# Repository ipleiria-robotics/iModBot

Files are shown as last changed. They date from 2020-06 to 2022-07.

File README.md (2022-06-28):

# Apresentação do Projeto 
Este projeto iModBot consiste num robô modular de baixo custo que pode ser programado através de liguagem de programação por blocos e/ou através de linguagem C/C++. Este projeto dispõe de uma biblioteca para facilitar o controlo do robô. 

A programação por blocos divide-se em 4 níveis, para facilitar a aprendizagem do utilizadores. Os níveis são os seguintes:
 - Nível Iniciante -> É possível colocar o robô a efetuar uma terefa com 1 a 2 blocos.
 - Nível Normal -> O utilizador tem mais controlo sob o movimento do robô, dispõe apenas da função loop.
 - Nível Médio -> O utilizador pode agora colocar blocos na função Setup e Loop.
 - Nível Avançado -> O utilizador dispõe de todas as funções da biblioteca e necessita de configurar todos os aspetos do robô.
    
ROBOT

# Como transferir ficheiros do GitHub
No GitHub não é possível transferir qualquer ficheiro individualmente. É recomendado transferir todas as pastas e ficheiros presentes neste projeto. Para tal siga as instruções abaixo:

Comece por transferir todos os ficheiros no formato .zip


Abra a localização do ficheiro .zip transferido e use um programa para extrair os conteudos


Por fim irá obter um conjunto de pastas e ficheiros organizados da mesma maneira que se encontram neste repositório.



# Elaboração do Projeto
**1º Passo do Projeto**

Para montar o robô basta seguir o documento 4_Guia_de_montagem_offline ([3_Documentacao/3-4_Guia_de_montagem_offline.pdf](https://github.com/ipleiria-robotics/iModBot/blob/master/3_Documentacao/3-4_Guia_de_montagem_offline.pdf)) que mostra como montar ou então assistir o video [iModBot@ipleiria.pt guia de montagem](https://www.youtube.com/watch?v=i4wFh0GqzkM&feature=emb_logo). Este documento também inclui uma listagem de componentes
que serão necessários para a sua montagem. Para perceber melhor o que faz cada componente do robô pode ler o manual técnico ([3_Documentacao/3-5_Manual_Tecnico_iModBot.pdf](https://github.com/ipleiria-robotics/iModBot/blob/master/3_Documentacao/3-5_Manual_Tecnico_iModBot.pdf)) que explica vários aspetos do robô. 

Lista de material:
 * ESP32 wroom32 devkit ; 
 <p align="center">
  
</p>

 * l293d 4 channel module ;
 <p align="center">
  
</p>   

 * 2x LM393 speed sensor ; 
 <p align="center">
  
</p> 

 * BFD-1000 5CH ;
  <p align="center">
  
</p>   

 * HC-SR04 ;
  <p align="center">
  
</p> 

 * I2C level shifter ; 
 <p align="center">
  
</p> 

 * TP4056 ; 
 <p align="center">
  
</p> 

 * MT3608 ; 
 <p align="center">
  
</p> 

 * li-ion rechargable battery 2500 mAh ; 
 <p align="center">
  
</p> 

 * 2x Breadboard 400 ; 
 <p align="center">
  
</p> 

 * Jumper wire male male, Jumper wire male female ; 
 <p align="center">
  
</p> 

 * 2wd smart robot kit . 
 <p align="center">
  
</p> 

**2º Passo do Projeto** 
 
 Downloads:
 
- Biblioteca iModBot.zip ([4_Biblioteca/iModBot.zip](https://github.com/ipleiria-robotics/iModBot/blob/master/4_Biblioteca/iModBot.zip)) e descompacta o ficheiro. Anotação 2020-06-25 170046

- Software Arduino IDE na [pagina do Arduino](https://www.arduino.cc/en/main/software), instale a versão que se adequa ao seu equipamento, para windows recomendamos a opção "Windows installer, for windows 7 and up". 
 -- Tenha em atenção que os conteudos do projeto foram desenvolvidos e testados na versão Arduino IDE 1.8.12, os mesmos deverão continuar ser compatíveis com as versões mais recentes deste software.
       <p align="center">
  
</p> 

- Ficheiro java do ArduBlock ([5_AduBlock/ardublock-beta-20200614.jar](https://github.com/ipleiria-robotics/iModBot/blob/master/5_AduBlock/ardublock-beta-20200614.jar)).

Anotação 2020-06-25 172512

**3º Passo do Projeto**

Ler e seguir os tutoriais para configurar o Arduíno:
 - Configurar Arduíno IDE para o ESP32; ([3_Documentacao/3-1_Como_comunicar_com_o_ESP32.pdf](https://github.com/ipleiria-robotics/iModBot/blob/master/3_Documentacao/3-1_Como_comunicar_com_o_ESP32.pdf))

 - Configurar ArduBlock no Arduíno IDE; ([3_Documentacao/3-2_Como_instalar_ArduBlock_no_Arduino_IDE.pdf](https://github.com/ipleiria-robotics/iModBot/blob/master/3_Documentacao/3-2_Como_instalar_ArduBlock_no_Arduino_IDE.pdf))

 - Como instalar bibliotecas no Arduíno IDE. ([3_Documentacao/3-3_Como_instalar_bibliotecas_no_Arduino_IDE.pdf](https://github.com/ipleiria-robotics/iModBot/blob/master/3_Documentacao/3-3_Como_instalar_bibliotecas_no_Arduino_IDE.pdf))

# Documentação

Após ter o Arduino IDE e o ArduBlock instalados pode usufruir dos tutoriais disponibilizados. Estes tutoriais ensinam a trabalhar com o robô sendo os mesmos divididos em duas categorias: tutoriais para ArduBlock e tutoriais para Arduino IDE.

**Documentação do ArduBlock**

Os [4 níveis](https://github.com/ipleiria-robotics/iModBot/tree/master/1_Tutoriais/1-1_Tuturiais_para_ArduBlock) a baixo irão facilitar e guiar como deve de utilizar cada bloco e como criar um programa.

- [Nivel Iniciante;](https://github.com/ipleiria-robotics/iModBot/blob/master/1_Tutoriais/1-1_Tuturiais_para_ArduBlock/Tutorial_1_-_Nivel%20iniciante/Nivel_iniciante.pdf)

- [Nivel Normal;](https://github.com/ipleiria-robotics/iModBot/blob/master/1_Tutoriais/1-1_Tuturiais_para_ArduBlock/Tutorial_2_-_Nivel_Normal/Nivel_Normal.pdf)

- [Nivel Médio;](https://github.com/ipleiria-robotics/iModBot/blob/master/1_Tutoriais/1-1_Tuturiais_para_ArduBlock/Tutorial_3_-_Nivel_Medio/Nivel_Medio.pdf)

- [Nivel Avançado;](https://github.com/ipleiria-robotics/iModBot/blob/master/1_Tutoriais/1-1_Tuturiais_para_ArduBlock/Tutorial_4_-_Nivel_Avancado/Nivel_Avancado.pdf)

Existe um conjunto de atividades para cada nível. Após ler a documentação de um nível poderá realizar a atividade correspondente  ao mesmo em [2_Atividades/2-1_Atividades_para_ArduBlock/](https://github.com/ipleiria-robotics/iModBot/tree/master/2_Atividades/2-1_Atividades_para_ArduBlock).

**Documentação do Arduino IDE**

Depois de já ter realizado os tutoriais do ArduBock deverá ter uma noção melhor de como programar no Arduino IDE. Também elaboramos alguns tutoriais e atividades para facilitar a aprendizagem,

- [Tutorial 1 - Movimento;](https://github.com/ipleiria-robotics/iModBot/blob/master/1_Tutoriais/1-2_Tutoriais_para_Arduino_IDE/Tutorial_1_-_Movimento/Tutorial_1_iModBot_-_Movimento.pdf)

- [Tutorial 2 - Sensores;](https://github.com/ipleiria-robotics/iModBot/blob/master/1_Tutoriais/1-2_Tutoriais_para_Arduino_IDE/Tutorial_2_-_Sensores/Tutorial_2_iModBot_-_Sensores.pdf)

- [Tutorial 3 - Seguir trajeto.](https://github.com/ipleiria-robotics/iModBot/blob/master/1_Tutoriais/1-2_Tutoriais_para_Arduino_IDE/Tutorial_3_-_Seguir_trajeto/Tutorial_3_iModBot_-_Seguir%20trajeto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)

As atividades para cada tutorial estão disponíveis em [/2_Atividades/2-2_Atividades_para_Arduino_IDE/
](https://github.com/ipleiria-robotics/iModBot/tree/master/2_Atividades/2-2_Atividades_para_Arduino_IDE).

# Editar o ArduBlock

Caso tenha interesse em criar um bloco deve seguir os passos neste pasta [5.Ardublock](https://github.com/ipleiria-robotics/iModBot/blob/master/5_AduBlock/README.md)

# Realidade Aumentada

Utilizando o motor de jogos Unity3d, ROS2 e a nossa biblioteca para o robô, cria o teu mundo virtual, projeta-o no mundo real e vê o robô a interagir com ele.
Esta funcionalidade ainda está em desenvolvimento sendo que por agora ainda é muito limitada. 

# Controladores remotos

Com os controladores das consolas populares PS3 e PS4, consegue controlar o robot à distância via bluetooth. A biblioteca é fácil de instalar e apenas necessita de um programa, o Arduino IDE. Basta colocar valores desejados no código, tanto como sensibilidade de direção, aceleração dos motores, velocidade máxima, e muito mais!

# Autores
 
- Abel Teixeira   - estudante do [Politécnico de Leiria](https://www.ipleiria.pt/cursos/) do curso TeSP em Eletrónica e Redes de Telecomunicações, GitHub: [Ab-Tx](https://github.com/Ab-Tx)
- Samuel Lourenço - estudante do [Politécnico de Leiria](https://www.ipleiria.pt/cursos/) do curso TeSP em Automação, Robótica e manutenção Industrial, GitHub: [SamueLourenc0](https://github.com/SamueLourenc0)
- Nelson Henriques - estudante do [Politécnico de Leiria](https://www.ipleiria.pt/cursos/) do curso TeSP em Automação, Robótica e manutenção Industrial, GitHub: [NetchoExtreme](https://github.com/NetchoExtreme)
- Paulo Sousa - estudante do [Politécnico de Leiria](https://www.ipleiria.pt/cursos/) do curso TeSP em Eletrónica e Redes de Telecomunicações, GitHub [DimitriOnLSD](https://github.com/DimitriOnLSD)

## Orientado por:
- Luís Conde - [Politécnico de Leiria](https://www.ipleiria.pt), GitHub: [Luís Conde](https://github.com/conde-ISR-UC-PT)
- Carlos Neves - [Politécnico de Leiria](https://www.ipleiria.pt), [INESC-Coimbra](http://inescc.estg.ipleiria.pt/), GitHub: [Carlos Neves](https://github.com/carlos-neves)

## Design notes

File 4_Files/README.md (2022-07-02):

# Files

Folder tree:
```
4_Files
├── 4-1_PCB_Files/        // 2 PCB versions
├── 4-2_3D_Files/         // Cases for the batteries and side motor supports
├── 4-3_Libraries/        // Dualshock libraries for remote controllers and iModBot library for various other functions
└── 4-4_ArduBlock/        // ArduBlock file for Arduino IDE and ArduBlock-Workspace for editing or creating blocks
```
## Software

To be able to edit source files inside the folders, you will need the following programs:

`Eclipse IDE` This is used to edit the ArduBlock-Workspace file. In there, you can edit or create blocks, change default values or create new ones, change blocks image, etc. Tutorials for installing this program, along with JDK and maven, can be found in the 3-Documents folder.

`EAGLE` This is used to open and edit the first PCB version. 

`Proteus 8.10` This is used to open and edit the second PCB version. Keep in mind that this file can't be opened in previous versions of proteus, like 8.9.

`Fusion 360` `SolidWorks` `SketchUp Pro 2021` These can be used to open and edit the .F3D, .step and .skp files inside Battery_Case_3D folder.

`Visual Studio Code` This is used to edit the .h and .cpp files inside both libraries.

`Arduino IDE` This is used to upload the code to the ESP32.

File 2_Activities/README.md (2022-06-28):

# Activities

Activities and their solutions are provided. 
These are divided into two categories:
- Activities for ArduBlock;
- Activities for Arduino IDE.

Tutorials for each activity are available at [1_Tutorials](https://github.com/ipleiria-robotics/iModBot/tree/master/1_Tutoriais)

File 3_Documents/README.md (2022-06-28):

# Documents

Inside this folder you will find documentation for the various project aspects and their respective DOCX files for editing:

- `src`
  - PDF source files.

- **3-00_iModBot_Components_List.xlsx**
  - Supplies the list components used in iModBot, with some of their respective buy stores and prices.

- **3-01_iModBot_Tech_Manual.pdf**
  - Describes the components used in the project, the functions provided by the library and other aspects.

- **3-02_iModBot_Assembly_And_Software_Installation_Tutorial.pdf**
  - Teaches you how to install the necessary tools and how to assemble the robot.

- **3-03_iModBot_Offline_Assembly_Guide.pdf**
  - Provides a list of components and shows the connections that must be made between the components.

- **3-04_Add_ESP32_Arduino_IDE.pdf**
  - Explains how to connect the ESP32 development board to the Arduino IDE software.

- **3-05_Add_ArduBlock_Arduino_IDE.pdf**
  - Explains how to install ArduBlock in the Arduino IDE software.
  
- **3-06_Add_Arduino_IDE_Libraries.pdf**
  - Explains how to install libraries in the Arduino IDE software.
  
- **3-07_Edit_ArduBlock_Files.pdf**
  - It teaches how to install all the tools needed to edit the ArduBlock Workspace.

- **3-08_Create_ArduBlock_Blocks.pdf**
  - Teaches how to create a block in ArduBlock using the Eclipse IDE.

- **3-09_Add_Eclipse_IDE_Libraries.pdf**
  - Explains how to add libraries to the Eclipse IDE software.

- **3-10_Update_JDK.pdf**
  - Guide to update the Java version for using the Eclipse IDE.

- **3-11_Openblock_Error_Tutorial.pdf**
  - Troubleshooting guide for error in openblocks install.

- **3-12_Basic_Eletronics_Assembly_Guide.pdf**
  - A basic assembly guide is provided to acquaint you with the Breadboard and how it works when mounting electronic boards in this tool.

- **3-13_Remote_Bluetooth_Dualshock.pdf**
  - A tutorial is provided on how to set up the code to pair a dualshock 3 or 4 controller to control the robot remotely via Bluetooth.

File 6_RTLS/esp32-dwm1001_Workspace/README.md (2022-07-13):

# esp32-dwm1001_Workspace

*Note that the examples below consist in very basic application using the UWB features of the DWM1001C. These examples are not intended to be used in a commercial application and may not comply with regulation requirements.*

*Advanced firmware for DWM1001C that would comply with regulations can be found on https://www.decawave.com/product/dwm1001-module/*

## Overview

This project contains C simple examples for DWM1001 hardware and its derivatives, such as the DWM1001-DEV board and Development Kit Board MDEK1001.

The DWM1001 module is a Ultra Wideband (UWB) and Bluetooth hardware based on DecaWave's DW1000 IC and Nordic Semiconductor nrF52832 SoC. It allows to build a scalable Two-Way-Ranging (TWR) RTLS systems with up to thousands of tags. 

The DWM1001-DEV is a development board for the DWM1001 module. It contains an integrated Jlink to facilitate development and debbuging.
For more information about DWM1001, please visit www.decawave.com.

The C simple examples allow user to discover the key functionalities offered by the DWM1001 and UWB. These examples are customized for DWM1001-DEV, and some modifications will be necessary to port them to other DWM1001 based hardware (in particular LED and button interface)

The project is built as follow : 
```
esp32-dwm1001_Workspace/
├── boards             // DWM1001-DEV board specific definitions
├── deca_driver        // DW1000 API software package 2.04 
├── examples           // C simple examples 
│   ├── ss_twr_init    // Single Sided Two Way Ranging Initiator example
│   ├── ss_twr_resp    // Single Sided Two Way Ranging Responder example
│   └── twi_accel      // LIS2DH12 accelerometer example with Two Wire interface 
├── nRF5_SDK_14.2.0    // Nordic Semiconductor SDK 14.2 for nrF52832
├── ESP32_UART_DWM1001 // UART communication interface with ESP32-DevKitC-V4
└── README.md
```
For more information about nrF52832 and nrF SDK, please visit http://infocenter.nordicsemi.com/

## Supported IDE

The examples are ready to use with the following IDE :
* Segger Embedded Studio (SES)
* Keil KEIL µVision

## Segger Embedded Studio

Each example contains a emproject project file for SES. The examples compile and load cleanly to the DWM1001.   
The project was created with the SES version V3.34a. 

SES has a free license for nrF52832 development. Consequently, this IDE can be used without any limitation for DWM1001 development.

For more information regarding Segger Embedded Studio, please visit https://www.segger.com/products/development-tools/embedded-studio/

For more information about free license for nrF52832, please read https://www.nordicsemi.com/News/News-releases/Product-Related-News/Nordic-Semiconductor-adds-Embedded-Studio-IDE-support-for-nRF51-and-nRF52-SoC-development

### SES : Additional Package

When using SES IDE, you will need to install the following package :

Package                                                                                                                           
CMSIS 5 CMSIS-CORE Support Package (version 5.02)                                                                           
CMSIS-CORE Support Package (version 4.05)                                                                           
Nordic Semiconductor nRF CPU Support Package (version 1.06)                                                                           

They can be install from SES itself, through the package manager in the tools menu. 

## KEIL µVision IDE

Each example contains a µVision5 project file for Keil µVision IDE. The examples compile and load cleanly to the DWM1001.
The project was created with the KEIL uVision version V5.24.2.0. 

Keil µVision has a free license for project up to 32KB. For more information regarding Keil µVision, please visit http://www2.keil.com/mdk5/uvision/

### µVision Error: Flash Download failed - "Cortex-M4"

This error can be observed if there is a memory conflict between the binary to load and the current firmware on the target hardware. This issue can be easily fixed by fully erasing the target device 's flash memory. Keil µVision cannot perform a full erase and the following free tool can be used :

* J-flash lite 
* nrfjprog command line script

For more information about the issue, please see :

https://devzone.nordicsemi.com/f/nordic-q-a/18278/error-flash-download-failed---cortex---m4-while-flashing-softdevice-from-keil-uvision-5

## Example Details 

The SS-TWR scheme can be implemented using two DWM1001 modules, the first one programmed as an initiator and the second one as a responder.

### Single Sided Two Way Ranging -- Initiator

This example contains the source code for the initiator. The initiator will send a frame, wait for the response from the receiver, calculate the distance and output it on the UART (can be observed on a serial terminal)

```
dwm1001-keil-examples/examples/ss_twr_init/
├── config                    // Contains sdk_config.h file for nrF SDK 14.2 customization
├── main.c                    // Initialization and main program
├── ss_init_main.c            // Single sided initiator core program
├── UART                      // Uart 
├── SES
│   └── ss_twr_init.emProject // Segger Embedded Studio project
└── Keil uvision
     └── ss_twr_init.uvprojx  // Keil uvision project

```
The application function is detailed in the main.c and the ss_init_main.c files. 

Calibration may be necessary in order to have an accurate measurement. It can be done by adjusting the antenna delay which is hardware dependent. 

### Single Sided Two Way Ranging -- Responder

This example contains the source code for the responder. The receiver will receive a frame from the initiator and send the corresponding answer.

```
dwm1001-keil-examples/examples/ss_twr_resp/
├── config                    // Contains sdk_config.h file for nrF SDK 14.2 customization
├── main.c                    // Initialization and main program
├── ss_resp_main.c            // Single sided responder core program
├── SES
│   └── ss_twr_resp.emProject // Segger Embedded Studio project
└── Keil uvision
     └── ss_twr_resp.uvprojx  // Keil uvision project
```
The application function is detailed in the main.c and the ss_resp_main.c files. 

Calibration may be necessary in order to have an accurate measurement. It can be done by adjusting the antenna delay which is hardware dependent. 

### Two Wire Interface Accelerometer

This example implements a TWI between the LIS2DH12 and the nrF52832. 
The blue led will be on when a motion is detected by the LIS2DH12. It also reports the accelerometer state on the UART.

```
dwm1001-keil-examples/examples/twi_accel/
├── config                    // Contains sdk_config.h file for nrF SDK 14.2 customization
├── LIS2DH12                  // LIS2DH12 (accelerometer) low level driver and api
├── main.c                    // Initialization and main program
├── TWI                       // TWI
├── UART                      // Uart
├── SES
│   └── twi_accel.emProject // Segger Embedded Studio project
└── Keil uvision
     └── twi_accel.uvprojx  // Keil uvision project
```
The application function is detailed in the main.c file.

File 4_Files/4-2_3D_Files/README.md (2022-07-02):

# 3D Battery cases

__Prototype 1__

`bat case v9.step`
Features the most recent version for single battery case for this prototype.

__Prototype 2__

`Battery_Holder.skp`
Features the most recent version for single battery case for this prototype.

`Battery_Holder_Stacked.skp`
Features an inside battery stacking with no middle layer. Simple use and faster printing but not recommended.

`Battery_Holder_Slot.skp`
Features an inside battery stacking with removable middle layer.

__Others__

`motors_side_support_v3.stl`
3D printable piece for side supports in iModBot chassis.

## Information

This folder contains all cases used in iModBot for the batteries. All outter holes dimensions are specifically designed for the iModBot chassis alone. 

Sterolithography files (STL) can be opened directly with CURA software for 3D printing. 

SketchUp (SKP), Fusion 360 (F3D) and Standard for the Exchange of Product Data (STEP) files are the given open-source files. SkethUp files were saved with 2021 version.

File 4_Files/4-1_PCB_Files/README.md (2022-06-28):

# PCB Files

__EAGLE__ and __KiCAD__

`iModBot_EAGLE_rev_1.rar`
First version of iModBot PCB with 1 battery input and Step-up to 7V.

`iModBot_EAGLE_REV_2.rar`
Second version of iModBot PCB with 2 batteries input, no Step-up and better organized schematic. This version does not include board files.

__Proteus 8.10__

`imodbot_rev_2.pdsprj`
PCB's first revision featuring an additional battery and removed the Step-up, with better testpoints.

`imodbot_rev_2-CADCAM.rar`
Contains CADCAM data for the proteus PCB.

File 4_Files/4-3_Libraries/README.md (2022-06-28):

# Dualshock and iModBot Libraries

These libraries were written in C/C++ programming language. You will find instructions on how to install these and upload them to the ESP32 inside the  [3-Documents](https://github.com/DimitriOnLSD/iModBot/tree/master/3_Documents) folder. Inside you can also find information regarding the robots' various functions.

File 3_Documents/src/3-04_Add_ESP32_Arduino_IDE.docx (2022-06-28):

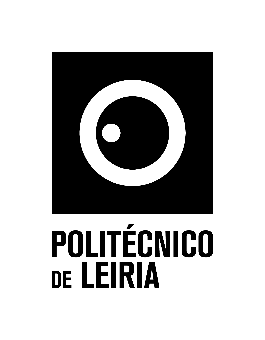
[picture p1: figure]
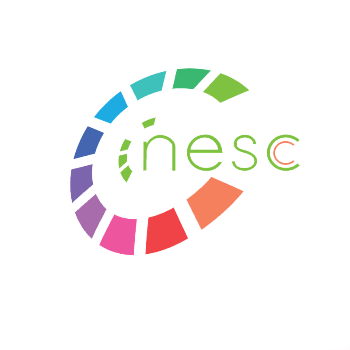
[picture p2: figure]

| Guia de montagem iModBot@ipleiria.pt

Tutorial de como comunicar com o ESP32 através do programa Arduíno IDE

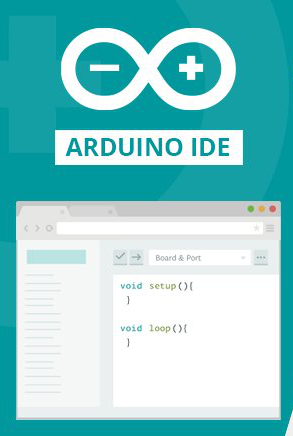
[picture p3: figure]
Tutorial of Programming ESP32 in Arduino IDE
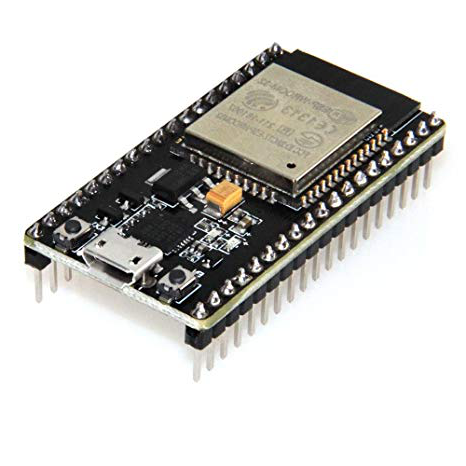
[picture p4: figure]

comunicar

Com o programa Arduino IDE aberto, siga os vários passos para configurar o Arduino IDE para comunicar o ESP32.

Também foi feito um vídeo para o caso de surgir alguma dúvida:

https://www.youtube.com/watch?v=xiqXJj58ynI

1. Com o Arduino IDE aberto, abra a janela “preferences” (File → Preferences);
2. Prima o botão que tem uma figura de uma pasta aberta (3) e cole o link:

https://dl.espressif.com/dl/package_esp32_index.json ;

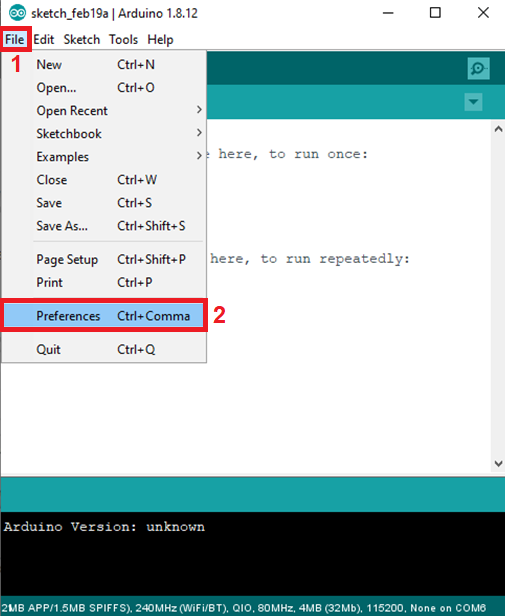
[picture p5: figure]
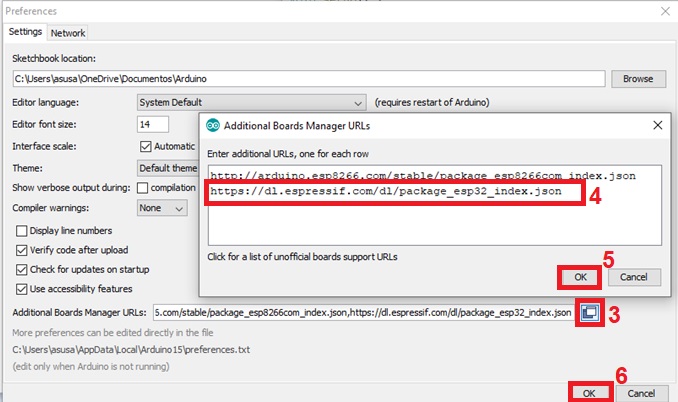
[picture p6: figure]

3. Na janela “Boards Manager…” escreva “ESP32” e instale a placa (Tools => Board=> Boards Manger…) ;

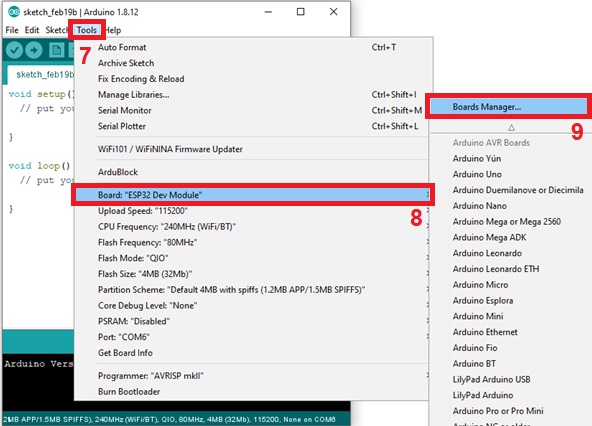
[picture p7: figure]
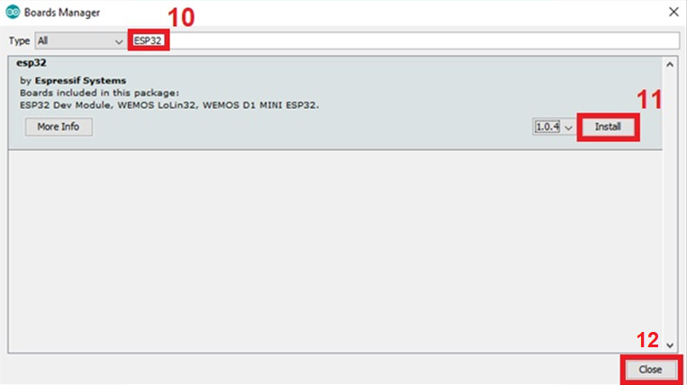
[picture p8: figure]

4. Ainda com a o separador “Tools” aberto configure os seguintes pontos:

“Board” escolha a placa compatível, neste caso “ESP32 Dev Module”;

“Upload Speed:” escolha uma das opções, é recomendado 115200;

“Port:” escolha a porta COM onde a placa de desenvolvimento ESP32 foi ligada, geralmente é o maior número apresentado;

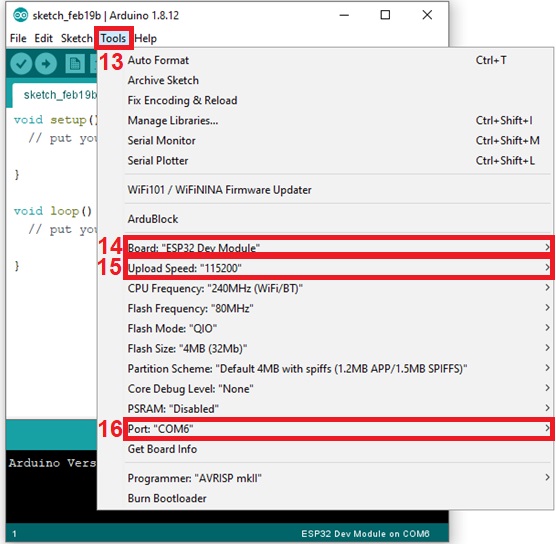
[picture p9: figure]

iModBot@ipleiria.pt Página 1 de 4

Autor: Samuel Domingos Lourenço 19 de fevereiro de 2020 2

Politécnico de Leiria 2019/2020

INSTITUTO POLITÉCNICO DE LEIRIA ESCOLA SUPERIOR DE TECNOLOGIA E GESTÃO

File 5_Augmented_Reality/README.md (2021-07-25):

# Realidade Aumentada

Utilizando o motor de jogos Unity3d, ROS2 e a nossa biblioteca para o robô, cria o teu mundo virtual, projeta-o no mundo real e vê o robô a interagir com ele.

Esta funcionalidade ainda está em desenvolvimento sendo que por agora ainda é muito limitada.

## Requisitos

 - Ubuntu 20.04 (nativo ou Virtual)
 -- Consulta o documento [Tutorial_SetUp_VM](https://github.com/ipleiria-robotics/iModBot/blob/master/6_Realidade_Aumentada/Tutorial_SetUp_VM.pdf) para o instalares numa Virtual Machine (é recomendado a instalação nativa).
 
  - Docker  
 -- Consulta o documento [Tutorial_docker](https://github.com/ipleiria-robotics/iModBot/blob/master/6_Realidade_Aumentada/Tutorial_docker.pdf) para o instalares e perceberes o seu funcionamento.

## Utilização

1. Abre um terminal na pasta [iModBot-Docker](https://github.com/ipleiria-robotics/iModBot/tree/master/6_Realidade_Aumentada/iModBot-Docker).
   
2. Cria a imagem Docker (este passo demora algum tempo).
    ```bash
    $ ./build-docker-image.bash
    ```
3. Inicia a imagem criada.
    ```bash
    $ ./run-docker-container
    ```
4.  Abre o `VScode`.
    ```bash
    $ code
    ```
	  --  Instala a  extensão PlatformIO e abre a pasta [VScode_Workspace\ESP32-ROS2_iModBot](https://github.com/ipleiria-robotics/iModBot/tree/master/6_Realidade_Aumentada/iModBot-Docker/VScode_Workspace/ESP32-ROS2_iModBot), coloca o id e a palavra pass da tua rede Wifi e o IP do container.
	  -- Faz Upload do programa para o ESP32.
	  -- Guarda as alterações e fecha o VScode.
    
5. Inicia o `Unity Hub` e instala o editor mais recente e abre o projeto que se encontra na pasta [iModBot-Docker\Unity_Workspace](https://github.com/ipleiria-robotics/iModBot/tree/master/6_Realidade_Aumentada/iModBot-Docker/Unity_Workspace/).
    ```bash
    $ cd unity && ./UnityHub.AppImage
    ```
6.  Inicia o ROS2 Node.
- No terminal da maquina nativa que se encontra na pasta iModBot-Docker abre um novo terminal no container.
    ```bash
    $ ./new_bash_in_container
    ```
 - No novo terminal:
    ```bash
    $ cd work/ROS2_Workspace && . install/setup.bash && ros2 run stop_oncollision oncollision
    ```
7. Inicia o controlo remoto (pode ser acedido em qualquer browser desde que esteja na rede local, através do IP que aparece na janela).
- Abre 2 novos terminais no container, como descrito anteriormente.
- No 1º:
    ```bash
    $ cd ros2-web-bridge && export DEBUG=ros2-web-bridge:* && node bin/rosbridge.js
    ```
- No 2º:
    ```bash
    $ cd ros2-web-bridge/demo && http-server -c-1
    ```
 
8. Inicia o MicroXRCEAgent (responsável por estabelecer a comunicação entre o ROS2 e o ESP32) 
- Abre um novo terminal no container.
- Inicia o programa
    ```bash
    $ MicroXRCEAgent udp4 -p 2018
    ```
Está tudo a postos para comecares a tua jornada com a realidade aumentada.
Sempre que quiseres reabrir o container corre o script [start-docker-container](https://github.com/ipleiria-robotics/iModBot/blob/master/6_Realidade_Aumentada/iModBot-Docker/start-docker-container.bash).

Video demostrativo: [https://youtu.be/DlAx3p5d99E](https://youtu.be/DlAx3p5d99E)

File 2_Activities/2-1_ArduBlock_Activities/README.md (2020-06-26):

# Atividades para ArduBlock

Os presentes tutoriais deverão facilitar a compreensão da linguagem de programaçãopor blocos bem como o seu uso no presente projeto.

Pode encontrar os tutoriais associados em [/1_Tutoriais/1-1_Tuturiais_para_ArduBlock/](https://github.com/ipleiria-robotics/iModBot/tree/master/1_Tutoriais/1-1_Tuturiais_para_ArduBlock).

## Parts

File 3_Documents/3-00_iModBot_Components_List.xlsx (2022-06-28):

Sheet: Previsão de custos_IPL
 |  | Dep. Eng. Eletrotécnica - UC de Projeto em Engenharia Eletrotécnica e de Computadores
 |  | Previsão de custos para Projeto
 |  | Título Projeto: | iModroBot
 |  | Orientadores: | Luis Conde Bento, Diogo Baptista, Alexandra Nascimento
 |  | Data: | 2020-12-09
 |  |  |  |  |  |  |  | Link principal
Item | Descrição | Referência | Qtd | Un. | Fornecedor | Preço unitário | Preço total
1 | Jetson Nano Developer Kit |  | 2 |  | sparkfun | 59.00 € | 59.00 €
2 | Espressif ESP32 WLAN Dev Kit Board Development Bluetooth Wifi v1 WROOM32 NodeMCU |  | 4 |  | ebay | 7.85 € | 31.40 € | https://www.ebay.com/itm/Espressif-ESP32-WLAN-Dev-Kit-Board-Development-Bluetooth-Wifi-v1-WROOM32-NodeMCU/253059783728
3 | Módulo De Accionamento Do Motor MINI L293D Arduino Accionamento Do Motor Placa De Expansão Mini-L293D Para Arduino Kit |  | 4 |  | dx | 3.96 € | 15.84 € | https://www.dx.com/p/mini-l293d-arduino-motor-drive-expansion-board-mini-l293d-motor-drive-module-for-arduino-kit-2716648.html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 | https://www.ebay.com/itm/Mini-Motor-Drive-Shield-Expansion-Board-L293D-Module-For-Arduino-UNO-MEGA2560-R3/182057002265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
4 | Placa de sensores infravermelhos IR 74HC14 |  | 4 |  | ptrobotics | 7.44 € | 29.76 € | https://www.ptrobotics.com/sensores-opticos/6248-5-channel-tracking-sensor-module.html
5 | 5Pcs Speed Measurement Sensor Switch Counter Motor Test Groove Coupler Module Geekcreit for Arduino - produtos que funcionam com placas oficiais Arduino |  | 8 |  | Banggood | 4.67 € | 37.36 € | https://pt.banggood.com/5Pcs-Speed-Measuring-Sensor-Switch-Counter-Motor-Test-Groove-Coupler-Module-p-953177.html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
6 | HC-SR04 Ultrasonic Ranging Module 4pin |  | 4 |  | ptrobotics | 3.69 € | 14.76 € | https://www.ptrobotics.com/sensor-ultrasom/4783-hc-sr04-ultrasonic-raging-module-4pin.html
7 | Carregador de bateria de lítio TP4056 com proteção Micro USB |  | 4 |  | solectroshop | 1.69 € | 6.76 € | https://solectroshop.com/pt/carregador-de-bateria/886-modulo-tp4056-carregador-de-bateria-de-litio-com-protecao.html
8 | 1pcs MT3608 2A DC-DC Adjustable Step Up Power Module Booster Power Module |  | 4 |  | Banggood | 1.22 € | 4.88 € | https://www.banggood.com/1pcs-MT3608-2A-DC-DC-Adjustable-Step-Up-Power-Module-Booster-Power-Module-p-1213134.html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
9 | Polymer Lithium Ion Battery - 3.7v 2500mAh |  | 4 |  | ptrobotics | 17.28 € | 69.12 € | https://www.ptrobotics.com/baterias-lipo/3096-polymer-lithium-ion-battery-3-7v-2500mah.html
10 | Breadboard 400 Point White |  | 8 |  | ptrobotics | 4.31 € | 34.48 € | https://www.ptrobotics.com/breadboards/3090-breadboard-400-points-white.html
11 | 40pcs 20cm Macho para Macho Cor Breadboard Cable Jump Fio Jumper |  | 4 |  | ptrobotics | 1.90 € | 7.60 € | https://pt.banggood.com/40pcs-20cm-Male-to-Male-Color-Breadboard-Cable-Jump-Wire-Jumper-p-992816.html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
12 | 40pcs 10cm Jump Wire Cabo de Ponte Macho para Fêmea para Arduino |  | 4 |  | ptrobotics | 1.69 € | 6.76 € | https://www.banggood.com/pt/40pcs-10cm-Male-To-Female-Jumper-Cable-Dupont-Wire-p-994063.html?gmcCountry=PT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
13 | Kit Carrinho Robot Arduino 2+1 Rodas 2WD Chassis |  | 4 |  | electrofun | 13.50 € | 54.00 € | https://www.electrofun.pt/robotica/kit-carrinho-robot-arduino-21-rodas-2wd-chassis
14 | 5 conjuntos de 4 Canais Bi-direcional Conversor de deslocador de nível lógico 3.3V-5V Para Arduino |  | 1 |  | ebay | 1.39 € | 1.39 € | https://www.ebay.com/itm/5Sets-4-Channel-Bi-Directional-Logic-Level-Shifter-Converter-3-3V-5V-For-Arduino/132880846914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
 | Previsão custo final |  |  |  |  |  | 373.11 €
Observações:
[1]
[2]
[3]
[4]

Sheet: Previsão de custos_PUBLICO
 |  | iModBot
 |  |  |  |  |  |  |  | Link auxiliar
Item | Descrição | Referência | Qtd | Un. | Fornecedor | Preço unitário | Preço total
2 | Espressif ESP32 WLAN Dev Kit Board Development Bluetooth Wifi v1 WROOM32 NodeMCU |  | 1 |  | ebay | 2.83 € | 2.83 € | https://www.aliexpress.com/item/32959541446.html
3 | Módulo De Accionamento Do Motor MINI L293D Arduino Accionamento Do Motor Placa De Expansão Mini-L293D Para Arduino Kit |  | 1 |  | dx | 1.07 € | 1.07 € | https://www.ebay.com/itm/L293D-Mini-Motor-Drive-Module-Shield-Expansion-Board-For-Arduino-UNO-MEGA2560-R3/123709591715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 | https://www.ebay.com/itm/Mini-Motor-Drive-Shield-Expansion-Board-L293D-Module-For-Arduino-UNO-MEGA2560-R3/182057002265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
4 | Placa de sensores infravermelhos IR 74HC14 |  | 1 |  | ptrobotics | 2.59 € | 2.59 € | https://www.banggood.com/5-Road-Tracing-Module-Tracing-Sensor-Module-5-Functions-Intelligent-Vehicle-Control-Module-p-1396250.html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
5 | 5Pcs Speed Measurement Sensor Switch Counter Motor Test Groove Coupler Module Geekcreit for Arduino - produtos que funcionam com placas oficiais Arduino |  | 2 |  | Banggood | 4.67 € | 9.34 € | https://www.ebay.com/itm/LM393-IR-Infrared-Speed-Sensor-Module-for-Arduino-AVR-PIC-RPI-3-3V-5V-207-/254266391545
6 | HC-SR04 Ultrasonic Ranging Module 4pin |  | 1 |  | ptrobotics | 3.69 € | 3.69 € | https://www.ebay.com/itm/HC-SR04-Ultrasonic-Wave-Detector-Ranging-Module-Distance-Measuring-PCB-4-Arduino/313271537687
7 | Carregador de bateria de lítio TP4056 com proteção Micro USB |  | 1 |  | solectroshop | 0.89 € | 0.89 € | https://www.ebay.com/itm/Ultrasonic-Module-HC-SR04-Distance-Measuring-Transducer-Sensor-For-Arduino-AVR/232379679409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
8 | 1pcs MT3608 2A DC-DC Adjustable Step Up Power Module Booster Power Module |  | 0 |  | Banggood | 0.38 € | 0.00 € | https://www.aliexpress.com/item/32970333618.html
9 | Polymer Lithium Ion Battery - 3.7v 2500mAh |  | 2 |  | ptrobotics | 4.66 € | 9.32 € | https://www.aliexpress.com/item/32966696278.html
10 | Breadboard 400 Point White |  | 2 |  | ptrobotics | 0.82 € | 1.64 € | https://www.aliexpress.com/item/32711841420.html
11 | 40pcs 20cm Macho para Macho Cor Breadboard Cable Jump Fio Jumper |  | 1 |  | ptrobotics | 0.74 € | 0.74 € | https://www.aliexpress.com/item/32825558073.html
12 | 40pcs 10cm Jump Wire Cabo de Ponte Macho para Fêmea para Arduino |  | 1 |  | ptrobotics | 0.74 € | 0.74 € | https://www.aliexpress.com/item/32825558073.html
13 | Kit Carrinho Robot Arduino 2+1 Rodas 2WD Chassis |  | 1 |  | electrofun | 4.93 € | 4.93 € | https://www.aliexpress.com/item/4000108827764.html
14 | 5 conjuntos de 4 Canais Bi-direcional Conversor de deslocador de nível lógico 3.3V-5V Para Arduino |  | 1 |  | ebay | 1.39 € | 1.39 € | https://www.ebay.com/itm/5Sets-4-Channel-Bi-Directional-Logic-Level-Shifter-Converter-3-3V-5V-For-Arduino/132880846914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
15 | Switch 3PDT |  | 1 |  | aliexpress | 1.36 € | 1.36 € | https://pt.aliexpress.com/item/32897629489.html?pdp_ext_f=%7B"sku_id"%3A"12000019925623104"%7D&pdp_npi=2%40dis%21EUR%21%211.36%21%21%21%21%21%402101e9d216558337290541957e3d61%2112000019925623104%21sea
 | Previsão custo final |  |  |  |  |  | 40.53 €
Observações:
[1]
[2]
[3]
[4]

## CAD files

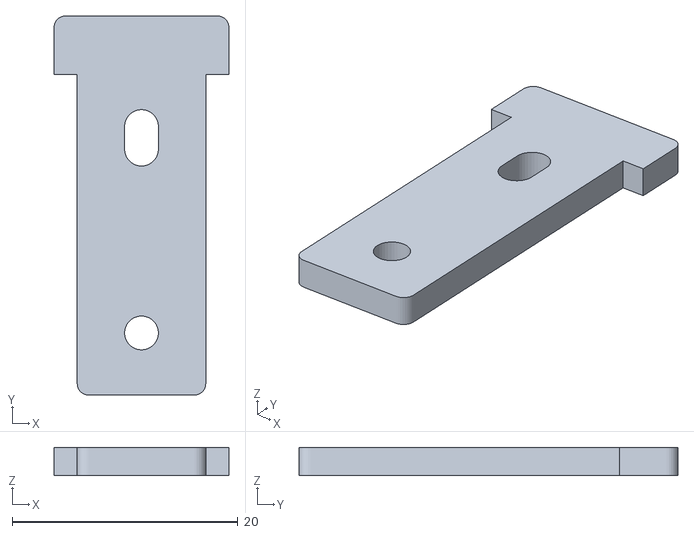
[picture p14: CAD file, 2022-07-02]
4_Files/4-2_3D_Files/motors_side_support_v3.stl
15.5 x 33.6 x 2.50

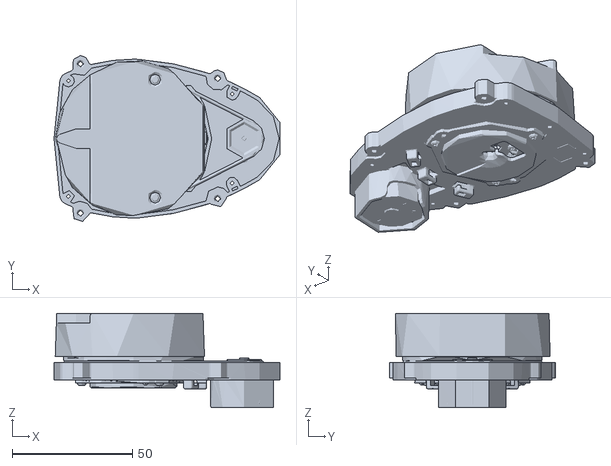
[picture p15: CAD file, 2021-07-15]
5_Augmented_Reality/iModBot-Docker/Unity_Workspace/iModBot-UnityRos2/Assets/ROS2/Robots/turtlebot3/turtlebot3_description/meshes/sensors/lds.stl
93.8 x 68.9 x 39.2

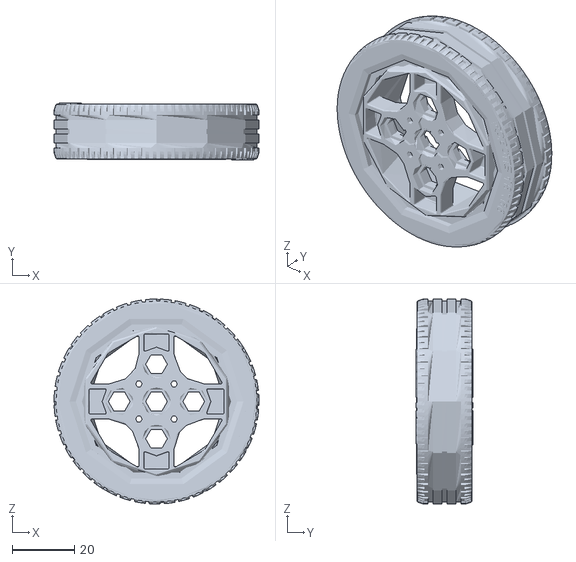
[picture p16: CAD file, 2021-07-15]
5_Augmented_Reality/iModBot-Docker/Unity_Workspace/iModBot-UnityRos2/Assets/ROS2/Robots/turtlebot3/turtlebot3_description/meshes/wheels/left_tire.stl
66.0 x 18.2 x 66.0

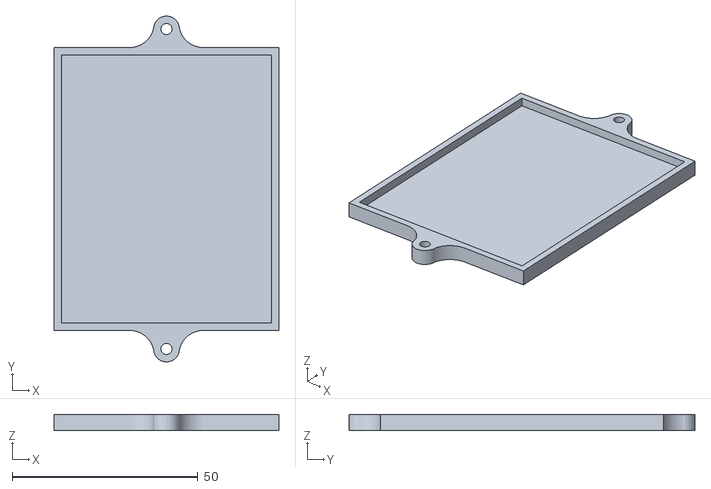
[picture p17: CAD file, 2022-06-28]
4_Files/4-2_3D_Files/Battery_Holder_Cover_V5.stl
60.5 x 93.2 x 4.40

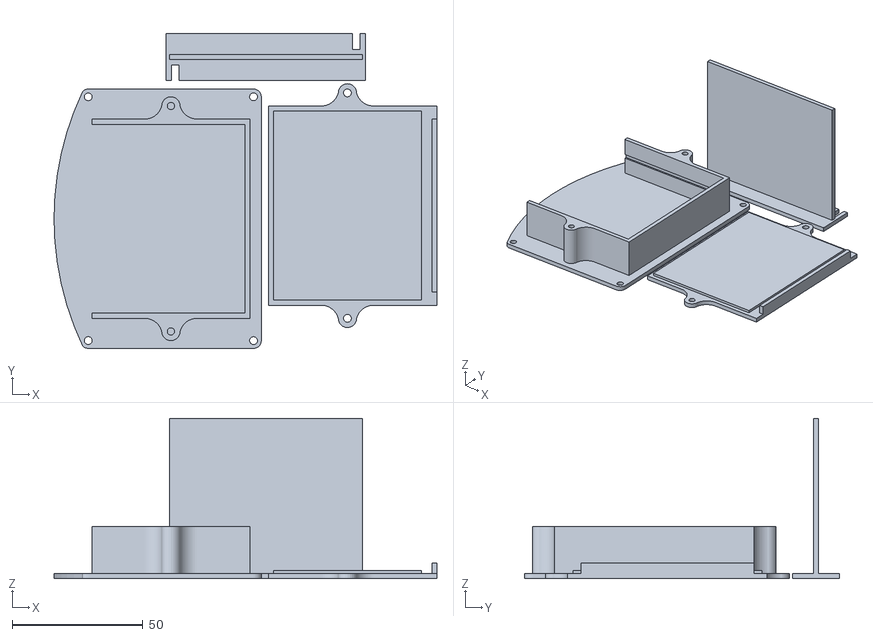
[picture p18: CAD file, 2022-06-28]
4_Files/4-2_3D_Files/Battery_Holder_Slot.stl
146.4 x 120.4 x 61.3

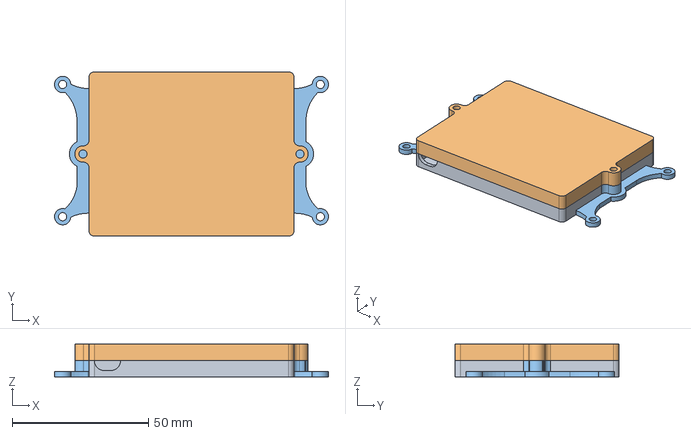
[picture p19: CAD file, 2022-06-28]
4_Files/4-2_3D_Files/bat case v9.step
100.7 x 60.4 x 12.0 mm

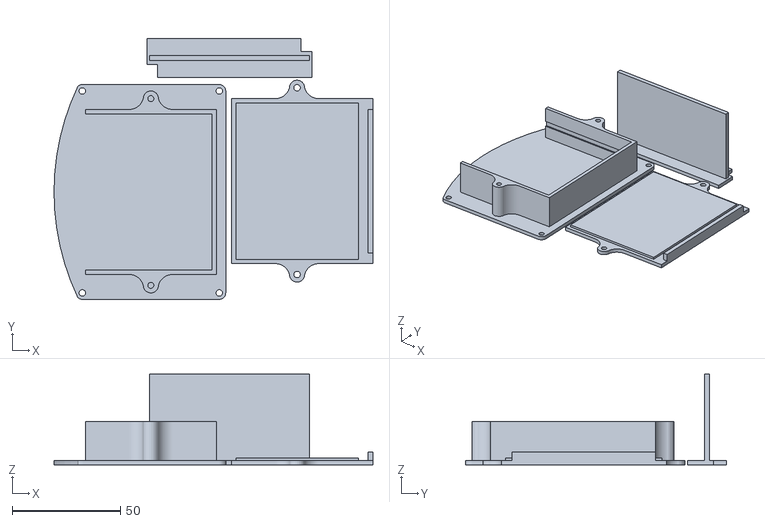
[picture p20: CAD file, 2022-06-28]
4_Files/4-2_3D_Files/Battery_Holder_Slot_V2.stl
147.2 x 120.4 x 42.0

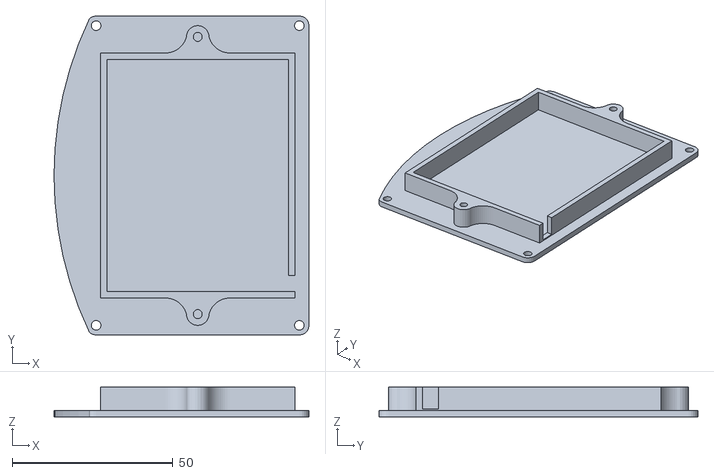
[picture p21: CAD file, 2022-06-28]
4_Files/4-2_3D_Files/Battery_Holder_V5.stl
79.3 x 99.2 x 9.20

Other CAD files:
5_Augmented_Reality/iModBot-Docker/Unity_Workspace/iModBot-UnityRos2/docker/turtlebot3_navigation/turtlebot3_description/meshes/wheels/right_tire.stl
5_Augmented_Reality/iModBot-Docker/Unity_Workspace/iModBot-UnityRos2/Assets/ROS2/Robots/turtlebot3/turtlebot3_description/meshes/wheels/right_tire.stl
4_Files/4-2_3D_Files/Battery_Holder.skp
4_Files/4-2_3D_Files/Battery_Holder_Slot.skp
4_Files/4-2_3D_Files/Battery_Holder_Stacked.skp
4_Files/4-2_3D_Files/bat case v9.f3d
5_Augmented_Reality/iModBot-Docker/Unity_Workspace/iModBot-UnityRos2/Assets/ROS2/Robots/crazyflie/crazyflie_description/meshes/crazyflie.skp

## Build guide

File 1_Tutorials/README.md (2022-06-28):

# Tutorials

Tutorials for ArduBlock contain educational content for block programming.

The tutorials for Arduino IDE contain educational content for C/C++ programming.

Activities are provided for each tutorial, they can be found in [2_Activities](https://github.com/ipleiria-robotics/iModBot/tree/master/2_Activities).

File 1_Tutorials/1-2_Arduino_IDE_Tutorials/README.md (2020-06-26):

# Tutoriais para Arduino IDE

Os presentes tutoriais deverão facilitar a compreensão da linguagem de programação C/C++ bem como o seu uso no presente projeto.

Pode encontrar as atividades associadas em [/2_Atividades/2-2_Atividades_para_Arduino_IDE/](https://github.com/ipleiria-robotics/iModBot/tree/master/2_Atividades/2-2_Atividades_para_Arduino_IDE).

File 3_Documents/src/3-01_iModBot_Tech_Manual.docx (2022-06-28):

# Manual Técnico iModRob@ipleiria.pt

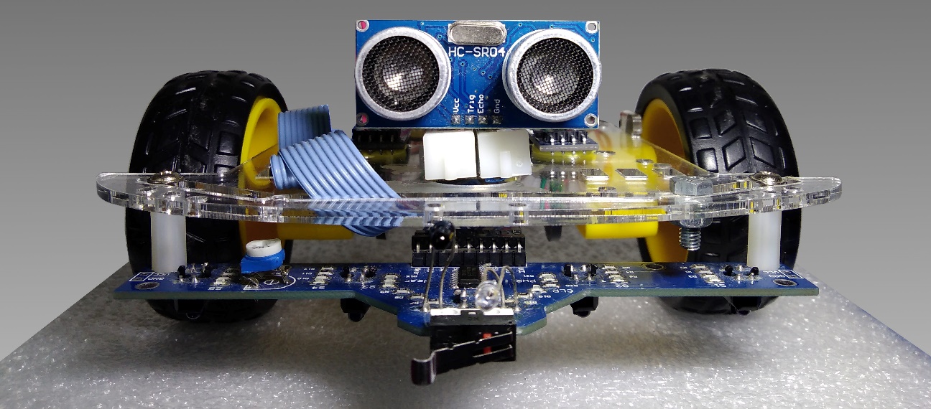
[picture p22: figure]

# Índice

# Introdução

O projeto iModBot@ipleiria.pt consiste num robô seguidor de linha, modular, de baixo custo.

É fornecida uma biblioteca escrita em C/C++ para facilitar o uso do mesmo.

Este robô pode ser programado através da aplicação Arduino IDE em linguagem C/C++ e também através de linguagem de programação por blocos utilizando o software ArduBlocks.

Neste documento serão descritos os componentes, as ligações dos mesmo e o uso da biblioteca.

# Descrição dos componentes

- DOIT ESP32 DevKit V1

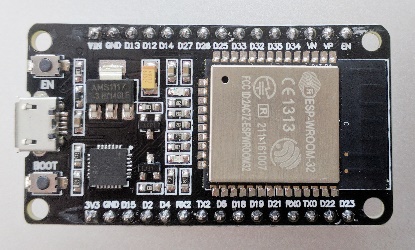
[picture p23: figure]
DOIT ESP32 DEVKIT V1 Board · Issue #544 · espressif ...

A placa de desenvolvimento DOIT ESP32 DevKit V1 irá controlar o robô e todos os seus periféricos. Esta placa é baseada no microcontrolador ESP32 desenvolvido pela Espressif Systems. Este microcontrolador possui uma velocidade de 80 até 240 MHz (dependendo da versão e/ou configuração), 4MB de memória flash e 520KB de SRAM.

Tensão de entrada do módulo: 5 a 12V.

Tensão de operação: 3.3V.

Wi-Fi: IEEE 802.11 b/g/n/e/i.

Bluetooth BLE.

- Módulo de controlo dos motores, L293D

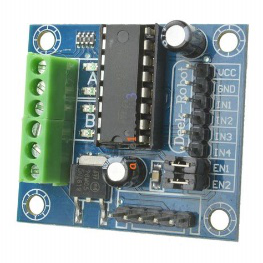
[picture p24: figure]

Este módulo servirá para controlar os motores.
No bloco terminal (VIN) pode ser conectada uma tensão de 7 até 35 V que irá alimentar o regulador 78M05 que por usa vez irá fornecer uma tensão de 5 V.
São necessários quatro pinos para controlar os dois motores, pode ser usada modulação de largura de pulsos (PWM) para controlar a velocidade dos motores.

Tensão de entrada no pino VIN: 7 a 35 V.

Corrente fornecida pelo 78M05: 500mA.

Nota: Forneça alimentação ao módulo apenas através do pino VIN. O pino VCC é uma saída e está conectado à saída do regulador 78M05 (presente na placa do módulo) que fornece 5 V.

- Placa de sensores IR 74HC14

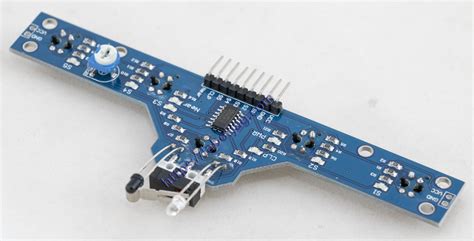
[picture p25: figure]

A placa de sensores infravermelhos possui seis emissores e seis recetores infravermelhos para possibilitar a deteção de linhas. Os recetores infravermelhos estão ligados a um inversor com histerese 74HC14 que irá evitar ruído nas ligações do mesmo à placa de desenvolvimento DOIT ESP32 DevKit V1. O sensor “Near” pode obter falsos-positivos devido à luz natural/ambiente.

A tensão de entrada (VCC) é de 2 a 6 V.

- Encoder Óticos

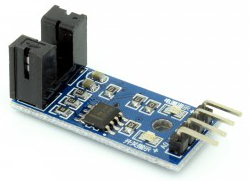
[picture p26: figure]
Motor Speed Encoder Sensor | Open ImpulseOpen Impulse

Os sensores óticos servem para obter um feedback da rotação das rodas podendo deste modo obter a distância percorrida e saber se uma está a rodar mais rapidamente que a outra.

Tensão de operação: 3.3 a 5 V.

- HC-SR04

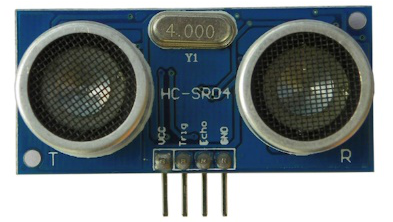
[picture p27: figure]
นาย arduino: ใช้ Arduino ติดต่อกับ Ping Ultrasonic Sensor ...

O sensor ultrassónico HC-SR04 permite detetar obstáculos com antecedência.

Tensão de operação: 5 V.

Consumo de corrente típico: 15mA.

Frequência de funcionamento: 40 MHz.

Alcance: desde 2cm até 4m.

Angulo de medição: 15º.

Tempo do sinal de gatilho: 10us nível TTL.

- Módulo de carga TP4056

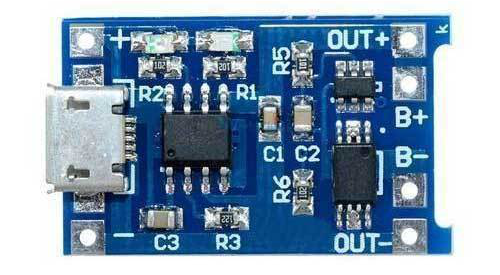
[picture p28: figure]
Lithium Ion Battery Charging Module TP4056, Voltage: 220 ...

O módulo baseado no circuito integrado TP4056 permite carregar baterias de iões lítio.
Possui um LED vermelho que indica que a bateria está a ser carregada e um LED azul que indica que o carregamento foi concluído.

Tensão de entrada: 4,5 a 8V.

Carrega a bateria até 4,2V ao máximo de 1A.

A potência de saída é a potência da bateria, tendo um máximo de 3 amperes limitado por um MOSFET.

- Módulo elevador de tensão MT3608

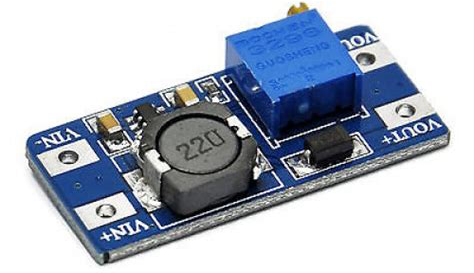
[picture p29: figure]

O módulo baseado no circuito integrado MT3608 efetua uma elevação de tensão ajustável.

A eficiência máxima é cerca de 93%, quanto maior for a diferença entre tensão de entrada/saída menor será a eficiência.

Tensão de entrada: 2 a 24 V.

Tensão de saída ajustável: 5 a 28V.

Corrente máxima fornecida (pico): 2A.

- Bateria de lítio de iões

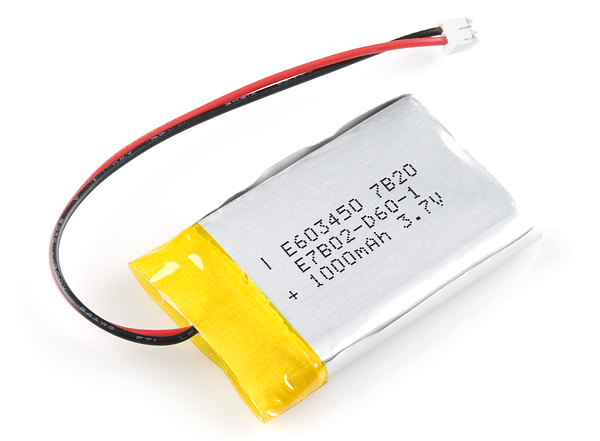
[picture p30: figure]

Para o projeto foi usada uma bateria de lítio de iões.

Este tipo de baterias são normalmente acessíveis e possuem bastante autonomia.

# Recursos do ESP32 usados pela biblioteca

A biblioteca iModBot usa os seguintes recursos do ESP32:

- 28 748 bytes de memória Flash (2,2%);
- Timer nº 0;
- Canais PWM nº 0, 1, 2 e 3;
- Canal nº 0 do periférico “Pulse Counter” nº 0;
- Canal nº 0 do periférico “Pulse Counter” nº 1.

# Descrição das funções da biblioteca

Nota: A contagem de pulsos dos enconder óticos é efetuada por hardware usando um módulo denominado de “pulse counter”. A configuração deste módulo encontra-se dentro das bibliotecas “E32_PC0” e “E32_PC1”. Quando a biblioteca “RobotOnLine” é usada estas outras duas bibliotecas serão incluídas automaticamente. Não é necessário incluir as bibliotecas “E32_PC0” e “E32_PC1” no programa que use a biblioteca “RobotOnLine”, o ambiente Arduino IDE poderá incluir as mesmas por defeito, estas inclusões pode ser apagadas.

- Void editWheelPin(uint8_t ,uint8_t )

Permite alterar os pinos onde são ligados os sensores óticos.

Se esta função for usada, a mesma deve ser chamada antes da função “begin()”.

Por defeito os pinos usados para os sensores óticos são o 26 e 27.

Os parâmetros são encoder da esquerda, encoder da direita respetivamente.

- Void editMotorPin(uint8_t ,uint8_t , uint8_t ,uint8_t ,)

Permite alterar onde são ligadas as conceções para controlar os motores.

Por defeito os pinos usados são o 2, 4, 16 e 17.

Os parâmetros são IN1, IN2, IN3, IN4 respetivamente.

- Void editUltrasonicPin(uint8_t ,uint8_t )

Esta função permite alterar os pinos que conectam ao sensor ultrassónico HC-SR04.

Por defeito os pinos usados são o 14 e o 12.

Os parâmetros são trig, echo respetivamente.

- Void editSensorPin(uint8_t ,uint8_t , uint8_t ,uint8_t , uint8_t ,uint8_t , uint8_t)

Permite alterar os pinos onde são estabelecidas as ligações à placa frontal que possui vários sensores de infravermelho.

Caso use a função de condução autónoma (seguir um trajeto de forma autónoma) da biblioteca, deve chamar esta função antes da função “beginAutoDrive();”

Por defeito os pinos usados são 25, 33, 32, 35, 34, 39, 36.

Os parâmetros são S1, S2, S3, S4, S5, CLP, Near respetivamente.

- Void setStopDistance(byte )

Esta função é destinada à funcionalidade de condução autónoma e permite definir a distância à qual o robô para. Quando encontra um obstáculo.

Por defeito a distância é 9cm. O número especificado de 0 a 255 é interpretado em centímetros,

- Void begin()

Esta função necessita de ser executada uma vez para iniciar a biblioteca e configurar os pinos e periféricos usados.

- Void beginAutoDrive()

Esta função é destinada à funcionalidade de condução autónoma e necessita de ser chamada uma vez para configurar as interrupções associadas aos sensores S2, S3, S4 e CLP. Quando esta função for chamada o robô irá verificar qual o valor de PWM mínimo para colocar ambas as rodas em movimento.

- Void endAutoDrive()

Esta função é destinada à funcionalidade de condução autónoma e necessita de ser chamada uma vez para desassociar as interrupções previamente configuradas pela função beginAutoDrive().

- byte autoDrive(byte)

Esta função é destinada à funcionalidade de condução autónoma e necessita de ser chamada constantemente para efetuar várias tarefas.

Os valores devolvidos são os seguintes:

- “0”, nada a reportar;
- “1”, múltiplas linhas encontradas;
- “2”, obstáculo encontrado;
- “3”, não foram encontradas quaisquer linhas.

O valor inserido é a instrução a efetuar para quando é encontrada mais que uma linha ou algum obstáculo:

- “1”, rodar para a direita;
- “2”, rodar para a esquerda;
- “3”, se não houver obstáculo seguir em frente;
- “4”, retroceder.
- void disableCLP()

Esta função é destinada à funcionalidade de condução autónoma, necessita de ser chamada uma vez para ignorar as leituras do sensor CLP.

- void disableNear()

Esta função é destinada à funcionalidade de condução autónoma e necessita de ser chamada uma vez para ser ativada. A sua função é desativar a leitura do sensor Near.

- void disableUltrasonic()

Esta função é destinada à funcionalidade de condução autónoma, necessita de ser chamada uma vez para ignorar as leituras do sensor de ultrassons HC-SR04.

- void noLineDelay(uint )

Esta função é destinada à funcionalidade de condução autónoma. A sua função é especificar o tempo que o robô demora a parar após deixar de detetar qualquer linha. Por defeito o valor é 700ms, o valor inserido é interpretado em milissegundos.

- void setSpeeds(byte ,byte ,byte)

Esta função permite definir o valor dutty-cycle (8 bits) usado para as velocidades máxima, média e mínima respetivamente. Por defeito os valores usados são 255, 200 e 180.

- byte distance()

Esta função devolve o valor medido (em centímetros) pelo sensor de ultrassons HC-SR04. Devolve um valor entre (e incluindo) 0 a 255.

- void turnLeft(uint16_t )

Esta função permite fazer o robô rodar x graus para a esquerda.

Se for enviado um 0 o robô irá tentar rodar 90 graus. Se for enviado um valor acima de 360 o robô irá apenas rodar 360 graus.

Esta função irá ser efetuada usando a velocidade mínima necessária para mover as rodas, isto para evitar que uma (ou ambas) as rodas derrapem.

Quando esta função for chamada o robô irá verificar qual o valor de PWM mínimo para colocar ambas as rodas em movimento.

- void turnRight(uint16_t )

Esta função permite fazer o robô rodar x graus para a direita.

Se for enviado um 0 o robô irá tentar rodar 90 graus. Se for enviado um valor acima de 360 o robô irá apenas rodar 360 graus.

Esta função irá ser efetuada usando a velocidade mínima necessária para mover as rodas, isto para evitar que uma (ou ambas) as rodas derrapem.

Quando esta função for chamada o robô irá verificar qual o valor de PWM mínimo para colocar ambas as rodas em movimento.

- void steerLeft(byte )

Esta função faz com que o robô vire ligeiramente à esquerda sem parar de seguir em frente.

- void steerRight(byte )

Esta função faz com que o robô vire ligeiramente à direita sem parar de seguir em frente.

- void rotateLeft(byte )

Esta função faz o robô rodar para a esquerda com a velocidade determinada pelo Dutty-Cycle (Modelação de Largura de Pulso) inserido. Um valor Dutty-Cycle muito baixo pode não ser suficiente para iniciar o movimento.

- void rotateRight(byte )

Esta função faz o robô rodar para a direita com a velocidade determinada pelo Dutty-Cycle (Modelação de Largura de Pulso) inserido. Um valor Dutty-Cycle muito baixo pode não ser suficiente para iniciar o movimento.

- void stopMotors()

Esta função simplesmente pára ambos os motores.

- void forward(byte )

Faz o robô seguir em frente com a velocidade determinada pelo Dutty-Cycle (Modelação de Largura de Pulso) inserido. Um valor Dutty-Cycle muito baixo pode não ser suficiente para iniciar o movimento. Se o valor inserido for 0 o robô irá parar.

- void reverse(byte )

Faz o robô recuar com a velocidade determinada pelo Dutty-Cycle (Modelação de Largura de Pulso) inserido. Um valor Dutty-Cycle muito baixo pode não ser suficiente para iniciar o movimento. Se o valor inserido for 0 o robô irá parar.

- void leftWheel(short )

Esta função controla o motor esquerdo individualmente. Pode ser inserido um valor de -255 a 255, um valor negativo fará a roda esquerda recuar e vice-versa. Se for inserido o valor 0 o motor irá parar.

- void rightWheel(short )

Esta função controla o motor direito individualmente. Pode ser inserido um valor de -255 a 255, um valor negativo fará a roda direita recuar e vice-versa. Se for inserido o valor 0 o motor irá parar.

- void clearEncoderCount()

A contagem dos pulsos lidos pelos encoder óticos é feita por hardware usando um módulo do ESP32 denominado “Pulse Counter”, esta função coloca a contagem de ambos os encoder a zero.

- int16_t getLeftEncoderCount()

Esta função devolve o número de pulsos contados pelo encoder esquerdo.

- int16_t getRightEncoderCount()

Esta função devolve o número de pulsos contados pelo encoder direito.

- byte checkSensors()

Esta função efetua uma leitura digital de cada pino presente na placa de sensores IR na frente do robô. Devolve um byte cujos bits significam o seguinte:

  - bit 0: É “1” se o sensor "Near" detetar algo.
  - bit 1: É “1” se o botão CLP for pressionado, isto normalmente acontece quando o robô colide com algo.
  - bit 2: É “1” se o sensor mais à direita detetar uma linha.
  - bit 3: É “1” se o sensor se o sensor da direita detetar uma linha.
  - bit 4: É “1” se o sensor do meio detetar uma linha.
  - bit 5: É “1” se o sensor da esquerda detetar uma linha.
  - bit 6: É “1” se o sensor mais à esquerda detetar uma linha.
- bool readS1 (); bool readS2(); bool readS3; bool readS4(); bool readS5();

Permite ler o estado dos sensores S1, S2, S3, S4 e S5. Devolve o valor “0” se for detetada uma linha preta.

- bool readNear();

Devolve 1 se for detetado um obstáculo pelo sensor Near;

- bool readCLP();

Devolve o valor “1” se o botão (switch) for pressionado.

- Void enSpeedAdj();

Ativa a função de ajuste de velocidade das rodas com base na velocidade especificada, seja esta em em rotações por segundo (RPS), rotações por minuto (RPM) ou metros por segundo (M/S), pelo utilizador.

- Float getRightRPS();

Devolve um valor de tipo float que representa a velocidade da roda direita em rotações por segundo.

- Float getLeftRPS();

Devolve um valor de tipo float que representa a velocidade da roda esquerda em rotações por segundo.

- Float getRightRPM();

Devolve um valor de tipo float que representa a velocidade da roda direita em rotações por minuto.

- Float getLeftRPM();

Devolve um valor de tipo float que representa a velocidade da roda esquerda em rotações por minuto.

- Float getRightMS();

Devolve um valor de tipo float que representa a velocidade da roda direita em metros por segundo.

- Float getLeftMS();

Devolve um valor de tipo float que representa a velocidade da roda esquerda em metros por segundo.

- Void forwardRPS(float );

Permite colocar o robô a mover-se em frente à velocidade especificada (em rotações por segundo RPS).

- Void reverseRPS(float );

Permite colocar o robô a retroceder à velocidade especificada (em rotações por segundo RPS).

- Void rotateRightRPS(float );

Permite colocar o robô a rodar para a direita (sentido horário) à velocidade especificada (em rotações por segundo RPS).

- Void rotateLeftRPS(float );

Permite colocar o robô a rodar para a esquerda (sentido anti-horário) à velocidade especificada (em rotações por segundo RPS).

- Void forwardRPM(float );

Permite colocar o robô a mover-se em frente à velocidade especificada (em rotações por minuto RPM).

- Void reverseRPM(float );

Permite colocar o robô a retroceder à velocidade especificada (em rotações por minuto RPM).

- Void rotateRightRPM(float );

Permite colocar o robô a rodar para a direita (sentido horário) à velocidade especificada (em rotações por minuto RPM).

- Void rotateLeftRPM(float );

Permite colocar o robô a rodar para a esquerda (sentido anti-horário) à velocidade especificada (em metros por segundo m/s).

- Void forwardMS(float );

Permite colocar o robô a mover-se em frente à velocidade especificada (em metros por segundo m/s).

- Void reverseMS(float );

Permite colocar o robô a retroceder à velocidade especificada (em metros por segundo m/s).

- Void rotateRightMS(float );

Permite colocar o robô a rodar para a direita (sentido horário) à velocidade especificada (em metros por segundo m/s).

- Void rotateLeftMS(float );

Permite colocar o robô a rodar para a esquerda (sentido anti-horário) à velocidade especificada (em metros por segundo m/s).

- Void moveAt(byte, byte, float);

Função responsável por colocar o robô em movimento para a direção e velocidade especificadas.

O primeiro parâmetro (da esquerda para a direita) é a direção, podem ser enviados os seguintes valores:

    - “1”, coloca o robô a seguir em frente;
    - “2”, coloca o robô a rodar para a direita;
    - “3”, coloca o robô a recuar;
    - “4”, coloca o robô a rodar para a esquerda;
    - Um valor diferente que se encontre de 0 a 255 irá parar ambos os motores.

O segundo parâmetro especifica o tipo de unidade, podem ser enviados os seguintes valores:

    - “1”, em rotações por segundo (RPS);
    - “2”, em rotações por minuto (RPM);
    - “3”, em metros por segundo (M/S).

O terceiro parâmetro é a velocidade relativa à unidade especificada no segundo parâmetro.

# Esquema elétrico recomendado

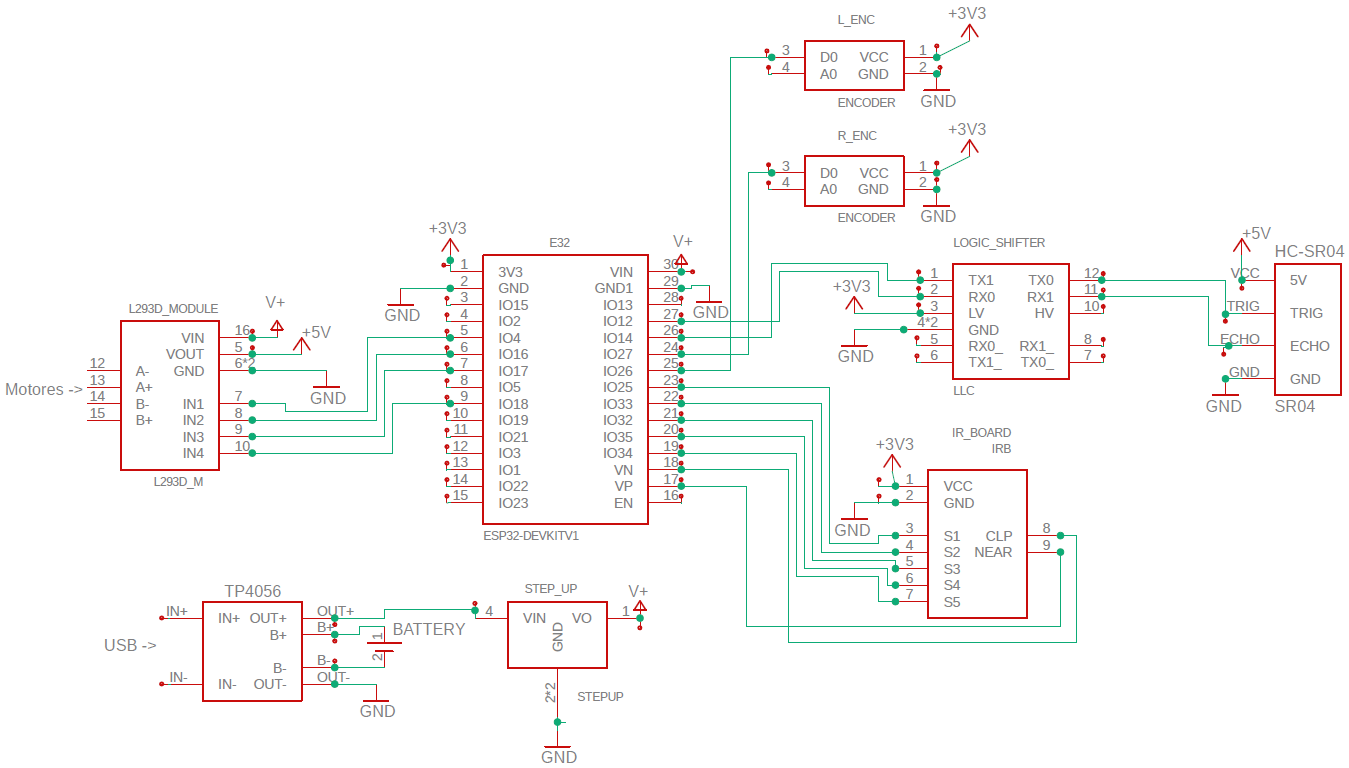
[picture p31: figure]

Figura 0.1 – Esquema

O esquema demonstrado na Figura 0.1 indica o esquema elétrico recomendado para o bom funcionamento do robô didático.

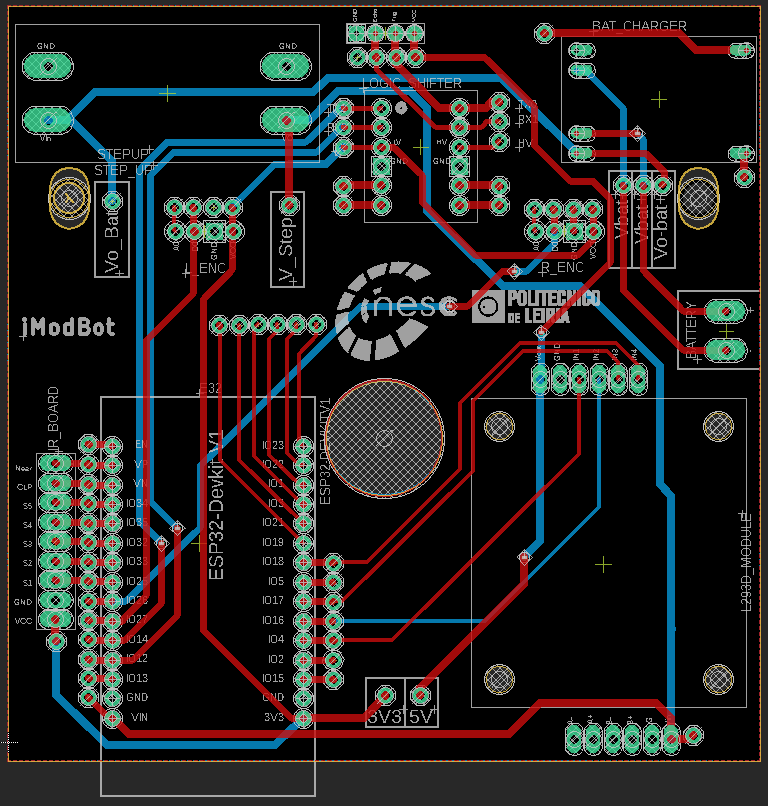
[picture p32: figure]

Figura 0.2 - Placa de Circuito Impresso

A Figura 0.2 exemplifica um possível layout da placa de circuito impresso criada a partir do esquema da Figura 0.1.

# Descrição do funcionamento da condução autónoma da biblioteca

Para efetuar a tarefa de seguir um trajeto de forma autónoma a biblioteca “RobotOnLine” recorre a duas funções principais, sendo uma delas associada a várias interrupções externas.

Função ”think()”

A função _think() é executada sempre que houver uma interrupção externa nos pinos conectados aos sensores S2, S3, S4 e CLP. Esta função, quando executada, desativa temporariamente as interrupções externas de modo a poder operar sem o risco de ocorrer um “loop” indeterminado.

Resumidamente a função “_think()” verifica se o robô embateu e a posição do trajeto (linha). Se não for encontrada nenhuma linha esta função irá copiar o valor da função “millis()” (esta função devolve o valor em milissegundos decorrido desde o inicio do programa) para uma variável global. Esta variável global será usada como uma “flag” e o valor da mesma será usado pela função “byte autoDrive(byte )” para parar o movimento do robô após um delay especificado. Quando o robô efetua uma curva poderão existir breves momentos em que a linha não seja detetada por nenhum dos sensores, daí a existência deste atraso na paragem do robô.

A função “_think()” também verifica se o robô chegou a um cruzamento. Para tal é que uma das seguintes combinações de sensores seja cumprida:

- S3 e S1 e S2 (sensores do meio e da esquerda);
- S3 e S4 e S5 (sensores do meio e da direita);
- S1 e S2 e S4 e S5 (sensores da direita e da esquerda).

Basicamente os sensores das bordas da placa são verificados de modo a ter a certeza de que o robô se encontra num cruzamento. Este processo foi implementado de modo a que o utilizador possa especificar o que o robô deve fazer quando este chega a um cruzamento.

A função “_think()” recorre a uma variável global denominada “_LLP” (abreviado de Last Line Position) para saber a ultima posição da linha, para evitar repetir instruções e para passar informação à função “byte autoDriver(byte )”.

Função “byte autoDrive(byte )”

A função “byte autoDrive(byte )” deve ser chamada o mais brevemente possível, pois esta é complementar à função “_think()” e executa várias tarefas. Esta função recebe e devolve valores, os valores devolvidos têm o seguinte significado:

- “0”, nada a reportar;
- “1”, múltiplas linhas encontradas;
- “2”, obstáculo encontrado;
- “3”, não foram encontradas linhas.

Caso seja encontrado um obstáculo ou múltiplas linhas (valor devolvido “1” ou “2”) podem ser enviados os seguintes valores para a função:

- “1”, o robô irá rodar para a direita até encontrar uma linha;
- “2”, o robô irá rodar para a esquerda até encontrar uma linha;
- “3”, caso não haja nenhum obstáculo, seguir em frente;
- “4”, retroceder.

É necessário enviar sempre um valor para a função, caso não seja intenção do utilizador dar uma instrução ao robô recomenda-se que envie o valor “0”. Apenas os números 1, 2, 3 e 4 dão instruções ao robô, qualquer outro número (até 255) não terá nenhum efeito.

A leitura dos sensores de ultrassons (HC-SR04) e sensor de infravermelho (Near) é efetuada nesta função.

A função “byte autoDrive(byte )” é responsável por fazer o ajuste da velocidade das rodas do robô, esta operação decorre de acordo com o seguinte fluxograma:

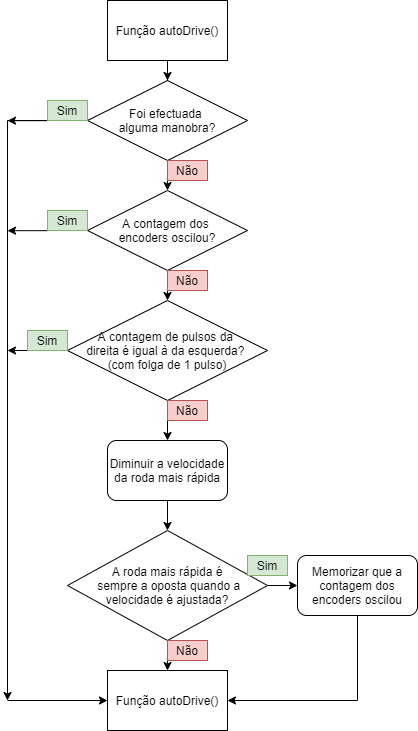
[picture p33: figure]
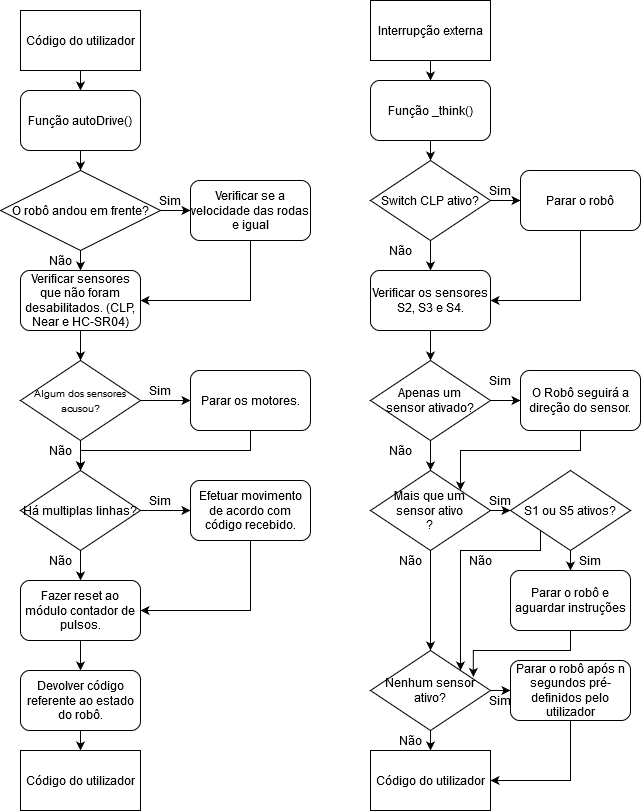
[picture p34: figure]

O seguinte fluxograma descreve o funcionamento de ambas as funções:

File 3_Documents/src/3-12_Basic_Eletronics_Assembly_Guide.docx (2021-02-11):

GUIA BASICA DE MONTAGEM DE CIRCUITOS ELETRICOS

O que é um circuito elétrico?

Em termos simples, é um caminho fechado pelo qual circula uma corrente elétrica numa mesma direção e de forma ordenada.

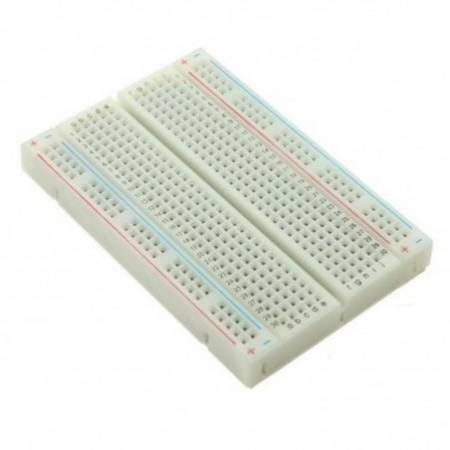
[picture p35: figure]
Placa ensaios Breadboard de 400 pontos

Um circuito elétrico pode estar composto por vários componentes e elementos, alguns mais necessários que outros, como a fonte de tensão, a massa e os cabos. O funcionamento de determinado circuito vai depender em grande medida dos componentes a utilizar.

Breadboard típica

A montagem dos circuitos vai ser numa breadboard, conhecida também por outros nomes como protoboard ou placa de ensaios. A placa tem pequenos furos ou orifícios os quais estão ligados entre si por conexões condutoras. É um componente bastante simples de usar e que permite-nos montar e desmontar uma amplia diversidade de circuitos com facilidade.

É importante conhecer e perceber a direção na qual os componentes devem ser ligados porque caso contrário arriscamo-nos em cometer erros que vão impedir que o circuito funcione como deve ser. Os cabos condutores, que bem podem ser de cobre, fósforo ou estanho, vão estar distribuídos basicamente da seguinte maneira, segundo o patrão típico duma protoboard como a antes indicada. As linhas verticais são chamadas de buses na breadboard e vão representar as o positivo e o negativo, que em geral, se o utilizador o achar conveniente, ao positivo como a fonte de tensão e ao negativo como massa ou terra. As linhas horizontais são o campo onde vamos fazer as ligações dos circuitos e funcionam basicamente da seguinte maneira: uma linha horizontal representa o mesmo nó, pelo qual se juntarmos dois fios no mesmo ponto da linha, vai significar que estão ligados entre si. Se fizermos ao contrário, é dizer, ligar um fio num ponto da horizontal e outro numa linha horizontal diferente, estes não vão estar ligados entre si.

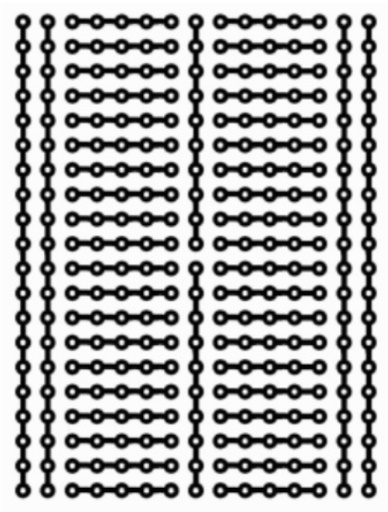
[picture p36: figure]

Uma sugestão ao momento de armar o circuito seria fazê-lo de forma organizada, com fios pequenos, evitando fiação aérea pois resulta mais confuso de perceber em circuitos mais complexos.

Circuitos Elétricos Básicos

- Ligação Serie

Uma ligação série basicamente segue um mesmo caminho para a passagem de corrente. No seguinte exemplo temos três resistências ligadas em serie com uma fonte de tensão. As setas representam a corrente que percorre um único caminho.

Cada um dos números apresentados na imagem a seguir, representa uma linha de pontos como está apresentado na figura de montagem de circuito, assim fazemos uma ligação em serie.

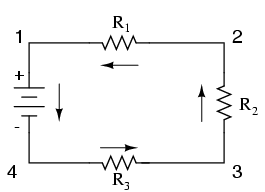
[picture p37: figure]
Circuito resistivo en serie - Análisis de circuitos I

Esquema de circuito serie

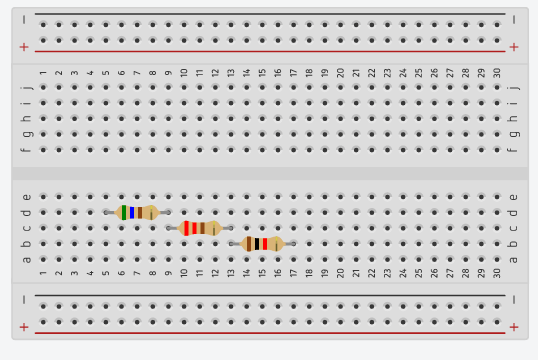
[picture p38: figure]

Montagem de circuito serie

Exemplos:

Neste caso, temos um circuito com quatro diodos led e uma resistência em serie alimentados por uma bateria.

Exemplo de ligação de resistências em série

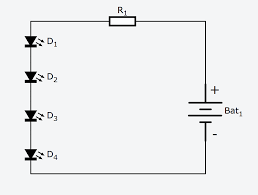
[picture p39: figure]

Esquema de circuito serie Circuito série na breadboard

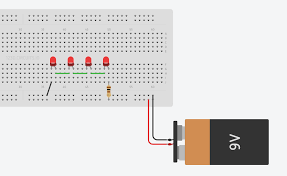
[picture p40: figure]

Ligação Paralelo

Uma ligação em paralelo consiste em que os componentes elétricos coincidam em cada um dos seus extremos, é dizer, a sua saída com a sua saída e a sua entrada com a sua entrada.

Como podemos ver no esquema de circuito paralelo, partilham um ponto numa parte das três diferentes resistências, e outro ponto diferente para a outra parte das três resistências. Como podemos ver na imagem da montagem de circuito paralelo estão ligadas três resistências numa mesma linha de pontos para a parte de acima do circuito e outra diferente linha de pontos para a outra parte das resistências.

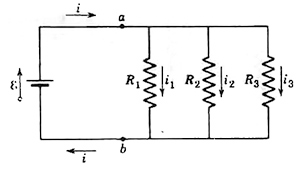
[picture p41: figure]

Esquema de circuito paralelo

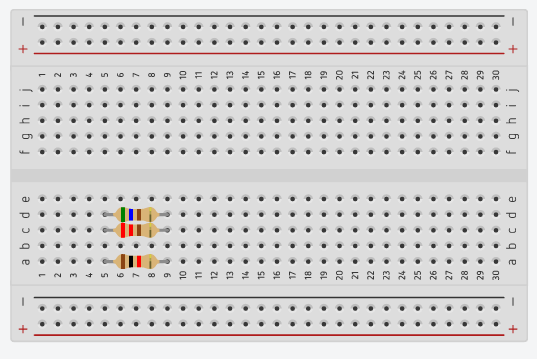
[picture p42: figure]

Montagem de circuito paralelo

Exemplos:

Neste caso, temos uma ligação paralela de 3 diodos LED com 3 resistências de proteção, na primeira imagem temos o esquema e na segunda temos a ligação na protoboard, como podemos ver, partilham uma linha de pontos interligados com fios e não diretamente, mas é indiferente para a perfeita execução do circuito.

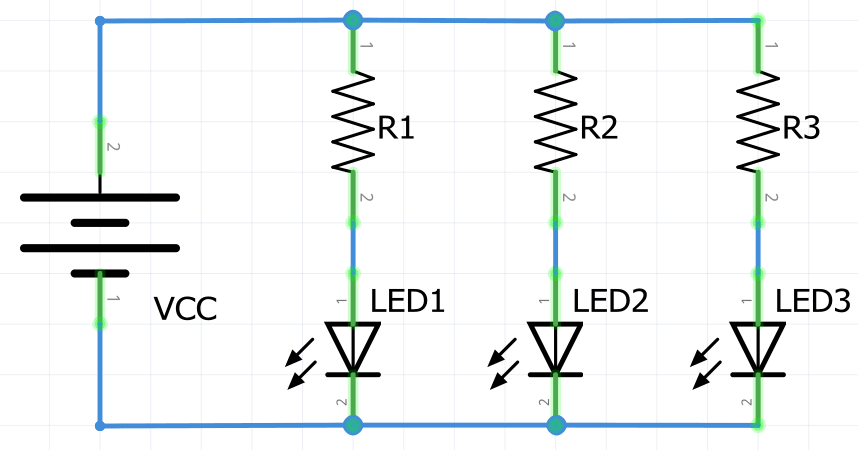
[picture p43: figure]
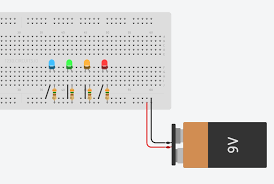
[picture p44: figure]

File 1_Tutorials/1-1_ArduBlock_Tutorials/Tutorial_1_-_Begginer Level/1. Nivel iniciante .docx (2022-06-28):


| Instituto de Engenharia de Sistemas e Computadores (INESC) de Coimbra Tutorial – Nível Iniciante

Programar o robô por blocos

iModBot (https://github.com/orgs/ipleiria-robotics/teams/imodbot-2020)

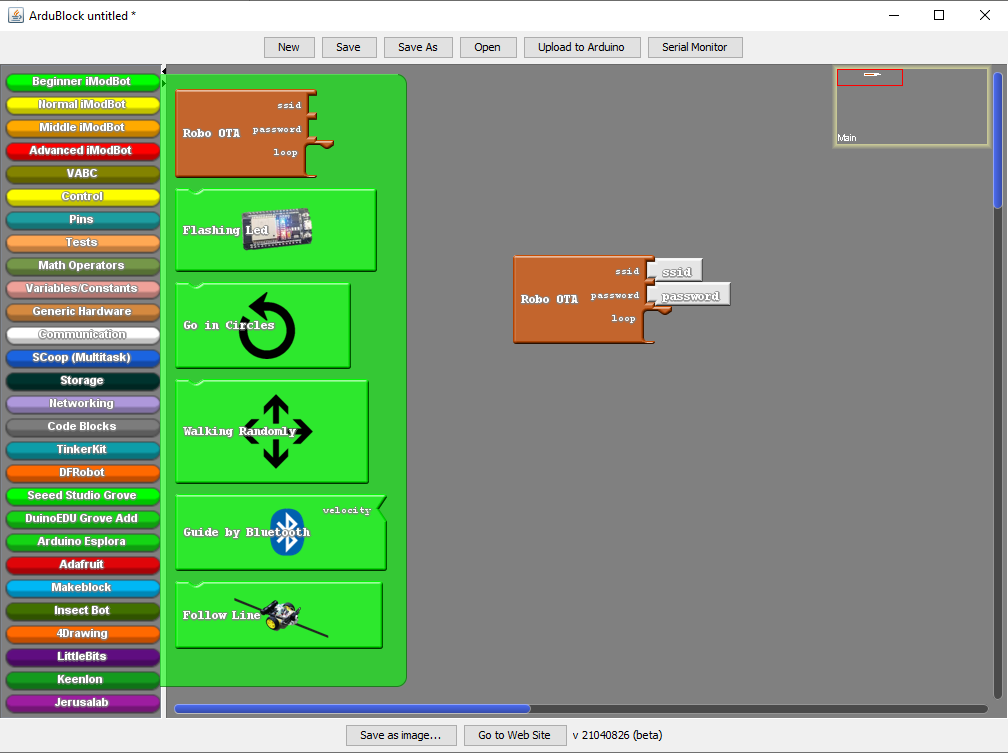
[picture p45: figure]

Alunos: Abel Teixeira - 2180522

Samuel Lourenço - 2180356

Docente: Carlos Neves

Luís Conde

Ano letivo: 2019/2020

# Abrir o ArduBlock

Se já tens o ArduBlock aberto pode saltar este passo e passar para o Nível Iniciante.

Caso ainda não tenha, comece por abrir o Arduíno IDE.

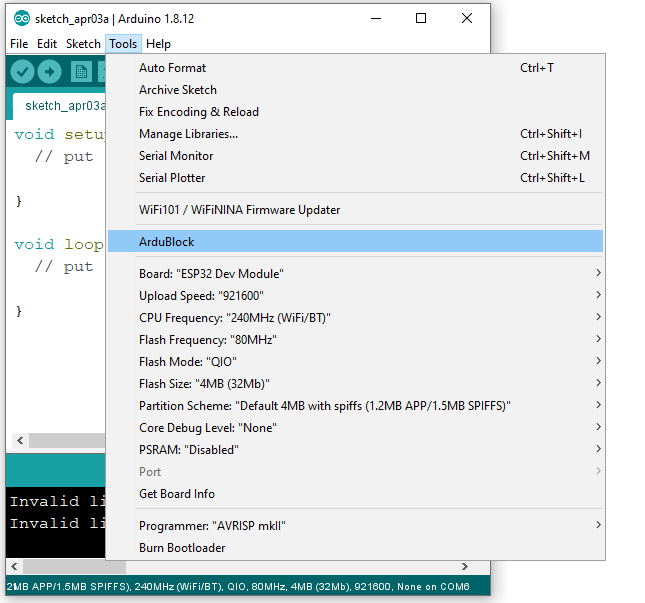
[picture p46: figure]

No Arduíno IDE clique “Tools” → “ArduBlock” e já tem ao ArduBlock aberto proto para contruir o programa.

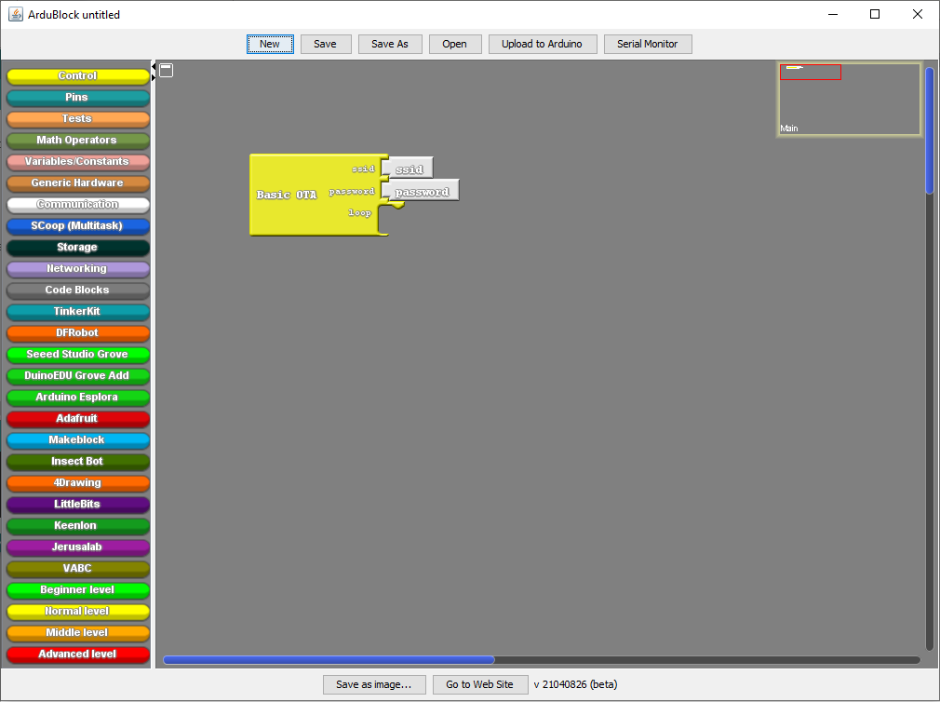
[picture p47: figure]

# Guia básico do ArduBlock

Este guia é para encenar o funcionamento básico do ArduBlock para o utilizador. Saber como utilizar e o nome de cada ferramenta.

O botão “Upload to Arduíno” converte o programa de blocos para linguagem C++ no Arduíno IDE.

O botão “Open” abre o programa que guardaram.

Os botões “Save” e “Save as” guarda o vosso programa onde o colocarem.

No botão “New” abre um novo ArduBlock.

O botão “Serial Monitor” aber uma janela onde mostra valores o que nós enviarmos para lá.

O botão “Go to Web Site” reencaminha-te para o site do ArduBlock, este link: http://blog.ardublock.com/ .

O botão “Save a image…” tira uma foto ao teu programa e guarda onde indicar.

Nesta coluna mostra as várias abas. Que ao clicar nelas mostra os blocos que tem dentro de cada uma.

Nós vamos começar por utilizar as 4 últimas abas.

Este retângulo mostra o vario espaço livre que tem para fazer o programa

Para eliminar algum bloco que não queiram basta arrentá-lo para cima da coluna das abas e largar e ele é eliminado do espeço de trabalho como pode ver na figura abaixo.

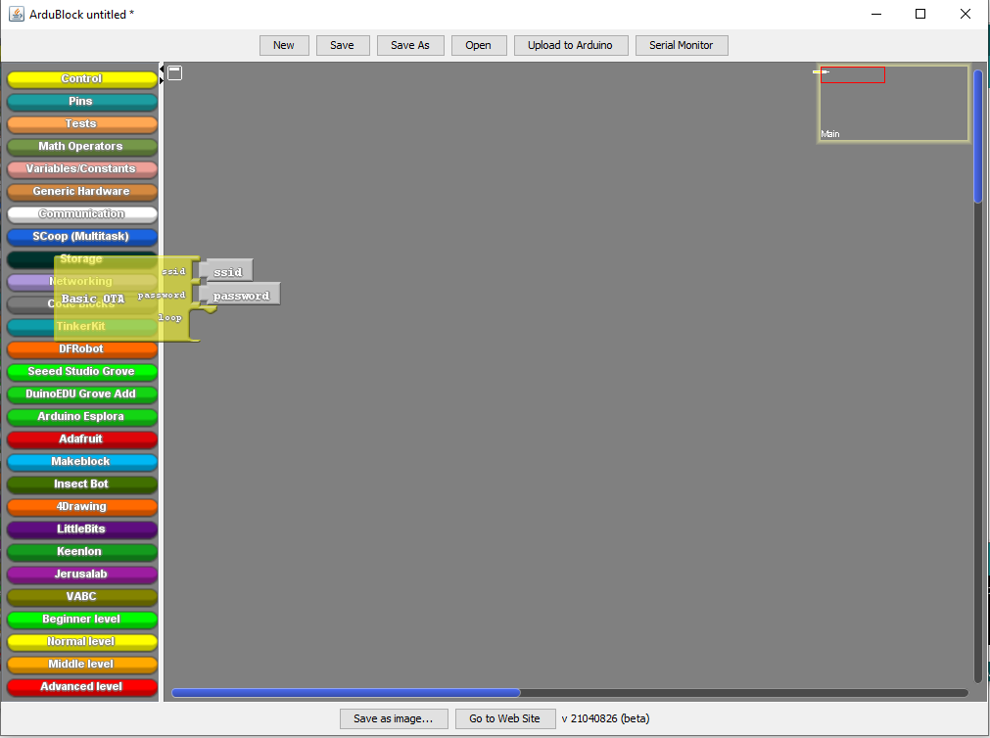
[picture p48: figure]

# Nível Iniciante (Beginner)

Neste nível basto só colocar um bloco no loop do bloco “Basic OTA”.

Caso não esteja ligado ao ESP32 com o cabo micro USB e queira ligar do wifi. Tem de clicar no bloco branco “ssid” e colocar o nome da internet e no bloco “password” colocar a passe da internet. Fica a comunicar com o ESP32 sem fios, sem esquecer da alimentação dele.

## 1. Bloco “Fashing Led”

Neste primeiro bloco verde vai fazer piscar o led azul que está ligado no pino 2. O objetivo é fazer piscar o led é para saber se o ESP32 está a comunicar por wifi. Para isso tem de abrir a aba verde com o nome “Beginner level” e arrastar o bloco “Fashing Led” para dentro do loop do bloco “Basic OTA”. Como podem ver na figura abaixo.

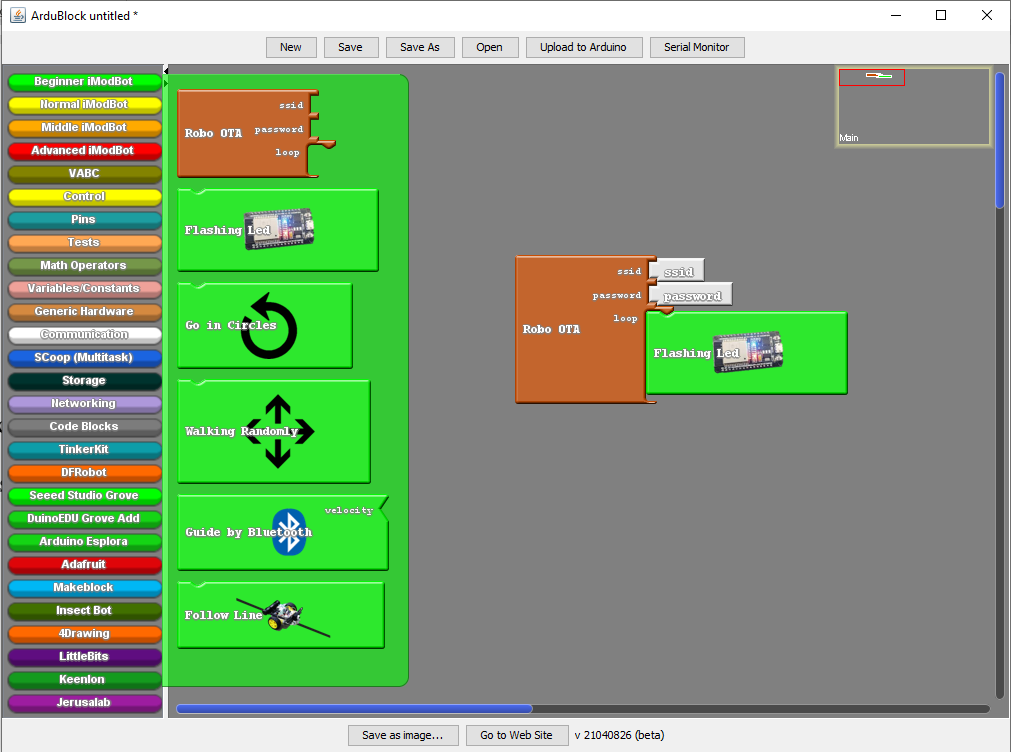
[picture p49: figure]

Não se esqueçam de colocar o “ssid” e a “password”. Depois clique no botão “Upload to Arduíno” que vai converter o programa que fizemos para a linguagem C++ no Arduíno IDE e envia para o ESP32. Que vais fazer piscar o led.

## 2. Bloco “Go in circles”

No segundo bloco verde o robô vai andar a roda. O objetivo é saber se as rodas estão bem ligadas. Para isso basta só colocar o bloco “Go in circles” no loop retirando o loco anterior.

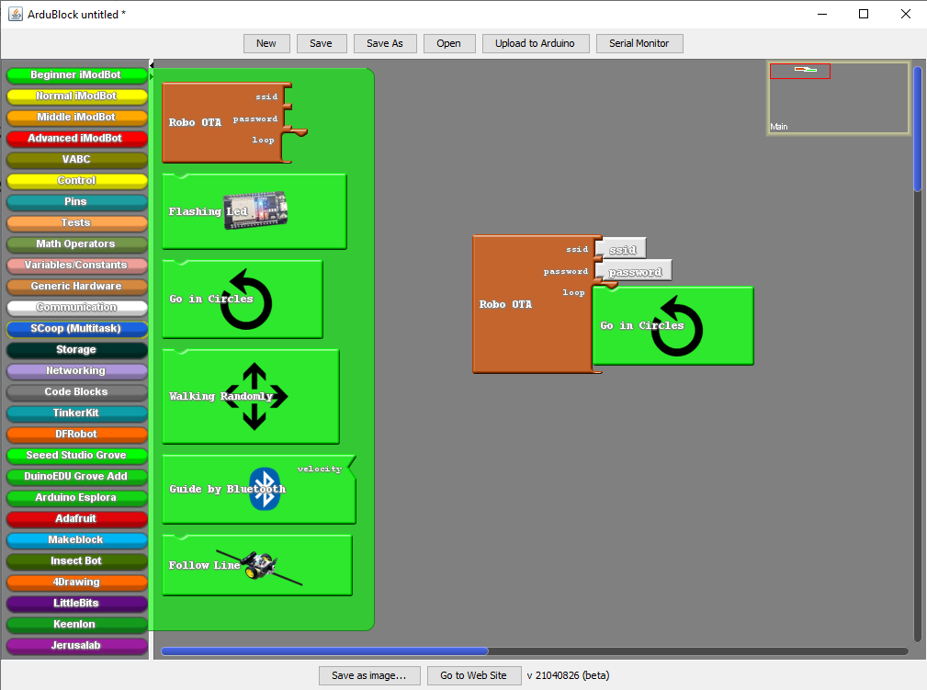
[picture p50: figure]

## 3. Bloco “Walking Randomly”

No terceiro bloco verde o robô vai andar aleatoriamente. O objetivo é saber se tá tudo bem ligado e as ordens do ESP32 (avançar, recuar, esquerda, direita e parar) estão a ser recebidas. Para isso basta só colocar o bloco “Walking Randomly” no loop retirando o loco anterior.

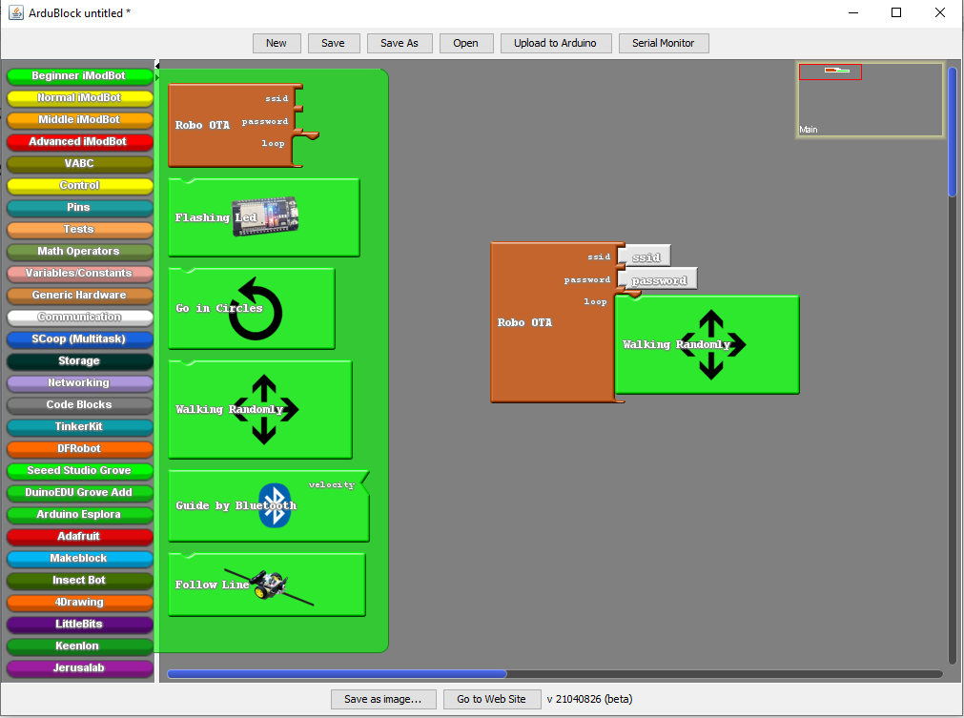
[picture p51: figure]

## 4. Bloco “Guide by Bluetooth”

No quarto bloco verde tem de tirar o bloco “Robo OTA” substituindo pelo bloco “Guide by Bluetoth” e definir a velocidade de 0 a 255. Como pode ver na figura abaixo.

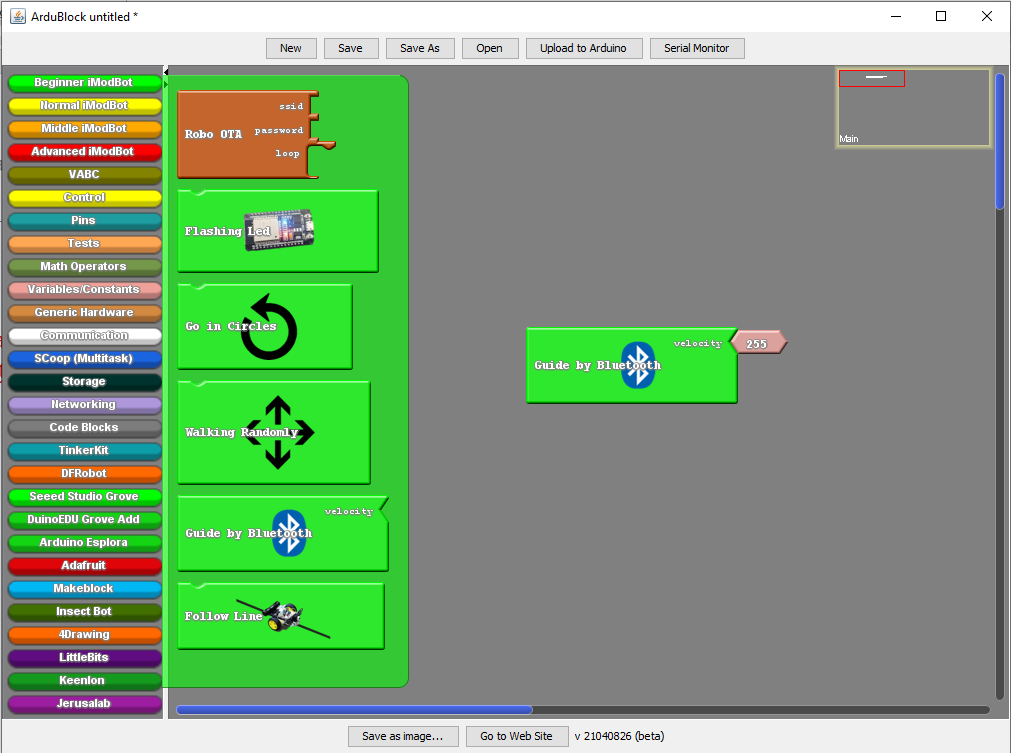
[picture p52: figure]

Depois de ter enviado para o ESP32, vai a “Play Store” do telemovel e procure por “Ultimate Bluetooth Joystick” e instale. Já com a aplicação intalada abrar e clique no icon no canto superior direiro parecido com uma roda dentada e clique em “Ajustar os botões”.

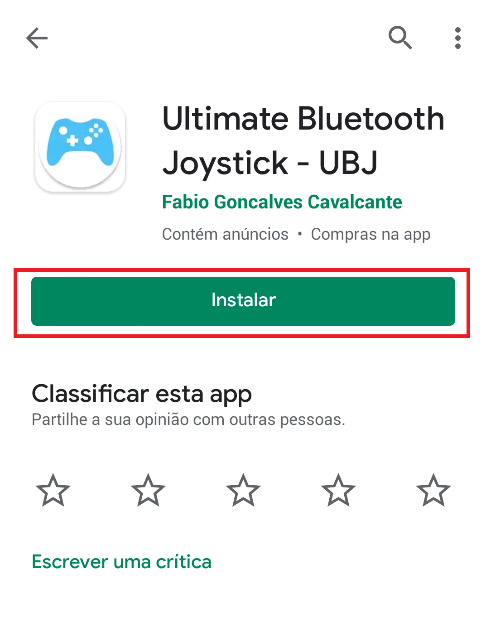
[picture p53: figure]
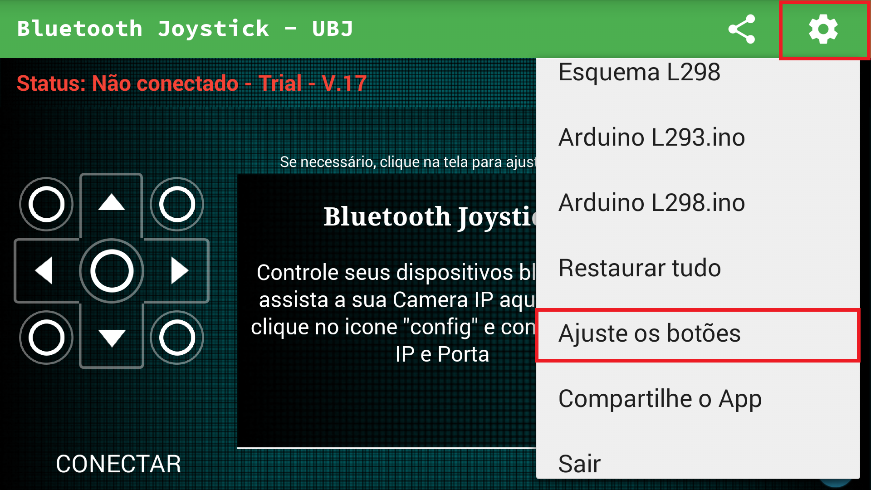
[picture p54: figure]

Clicam nas setas pretendida como mostra em baixo e alteram onde diz “Pressionado” e colocam a lenta consoante a seta, onde diz “Solto” retiram a letra e não colocam nada.

Nota: as letras tens de ser em minúsculas.

“a” – Avançar;

“b” – Virar à direita;

“c” – Virar à esquerda;

“d” – Recuar.

“e” até “z” – Pára o robô

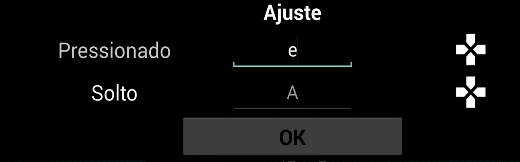
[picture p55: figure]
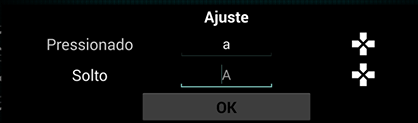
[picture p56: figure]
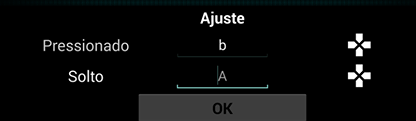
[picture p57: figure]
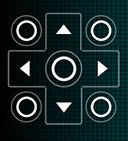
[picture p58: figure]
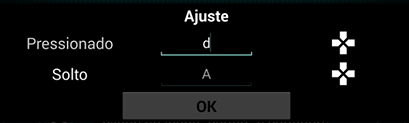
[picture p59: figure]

Já com a alteração feita clica “Parar a configuração”, e depois no “CONECTAR”. Vai abrir uma nova janela e pressionam em “Procurar” e escolhem o ESP32 e tá pontos para girarem o robô por Bluetooth.

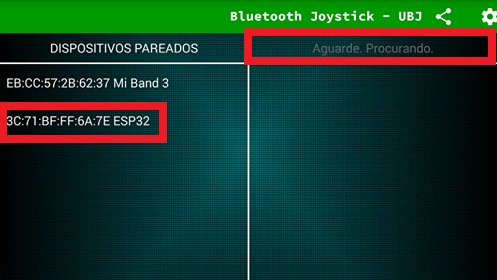
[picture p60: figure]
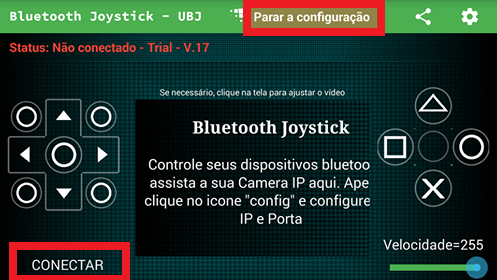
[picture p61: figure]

## 5. Bloco “Follow Line”

No quinto bloco verde o robô vai seguir a linha preta basta só colocar o bloco no loop e colocar o robô em cima da linha e ele vai seguir.


Nível Iniciante – iModBot@ipleiria.pt Página 30 de 30

Politécnico de Leiria 2019/2020

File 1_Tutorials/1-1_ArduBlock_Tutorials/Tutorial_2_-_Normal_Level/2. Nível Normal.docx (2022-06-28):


| Instituto de Engenharia de Sistemas e Computadores (INESC) de Coimbra Tutorial – Nível Normal

Programar o robô por blocos

iModBot (https://github.com/orgs/ipleiria-robotics/teams/imodbot-2020)


Alunos: Abel Teixeira - 2180522

Samuel Lourenço – 2180356

Docente: Carlos Neves

Luís Conde

Ano letivo: 2019/2020

# Nível Normal (Normal)

Neste nível ao contrário do anterior, o utilizado escolhe para onde o robô vai. Montado os blocos uns em cima dos outros, no espaço vazio do bloco castanho “Robot OTA”

1. Loop

## 1.1. Bloco “Define Speed”

Com este bloco define a velocidade que o robô vai andar. Escrevendo do bloco a frente 1 (150), 2 (200) ou 3 (255). Sendo que o número 3 corresponda ao 255 que é igual a 5V, a tenção máxima do ESP32

Nota: Este bloco tem de ser o primeiro.

## 1.2. Bloco “Right”

Ao colocar o bloco “Right” vai fazer com que o robô vire para a direita os graus que colocar no bloco.

## 1.3. Bloco “Left”

Ao colocar o bloco “Left” vai fazer com que o robô vire para a esquerda os graus que colocar no bloco.

## 1.4. Bloco “Advace”

Ao colocar o bloco “Advace” vai fazer com que o robô ande para frente os centímetros que colocar no bloco.

## 1.5. Bloco “Back Off”

Ao colocar o bloco “Back Off” vai fazer com que o robô recue os centímetros que colocar no bloco.

## 1.6. Bloco “Dodge Obstacles”

Ao colocar o bloco “Dodge Obstacles” vai fazer com que o robô ande para frente até que esteja a uma distância de um obstáculo. A distância é determinada pelo número que colocar no bloco a frente do “cm”.

## 1.7. Bloco “Run Once”

Este bloco “Run Once” vai fazer com que o programa dos blocos que colocar dentro deste só se repita uma vez. Sem este bloco, todo o programa dos blocos que colocar no loop iram se repetir várias vezes.

## 2. Exemplos de programa de blocos

Nestes exemplos vai perceber melhor como funcionam os blocos para programar o robô.

  2.1. Caminho em L

Começa com o bloco “Advance” faz andar 15 centímetros para a frente, bloco “Left” faz roda para a esquerdado robô 90 graus; o bloco “Advance” faz andar 10 centímetros para a frente. E como está dentro do bloco “Run Once” o robô só faz uma vez.


90º

10cm

15cm

  2.2. Caminho em L sem parar

Este exemplo é semelhante ao anterior só que neste o robô não parar.

- Bloco “Advance” faz andar 20 centímetros para a frente,
- Bloco “Left” faz roda para a esquerdado robô 90 graus;
- Bloco “Advance” faz andar 20 centímetros para a frente,
- Bloco “Left” faz roda para a esquerdado robô 90 graus;


Os quatro blocos amarelos fazem a primeira vez faça o caminho das setas preta e depois repete e fazendo o caminho da seta verde. Fazendo várias vezes, que faz o formato de um quadrado.

20cm

20cm

20cm

20cm

Nível Normal – iModBot@ipleiria.pt Página 1 de 7

Politécnico de Leiria 2019/2020

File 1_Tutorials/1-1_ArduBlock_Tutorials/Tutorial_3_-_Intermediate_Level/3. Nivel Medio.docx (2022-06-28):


| Instituto de Engenharia de Sistemas e Computadores (INESC) de Coimbra Tutorial – Nível Médio

Programar o robô por blocos

iModBot (https://github.com/orgs/ipleiria-robotics/teams/imodbot-2020)


Alunos: Abel Teixeira - 2180522

Samuel Lourenço – 2180356

Docente: Carlos Neves

Luís Conde

Ano letivo: 2019/2020

# Nível Médio (Middle)

No nível medio vai altera o bloco “Robo OTA” que só com loop para o bloco “Basic OTA” que está na aba “Middle level” para se começam a habituar ao modo de programação em C++.


## 1. Blocos dos Setup

Os quatro blocos a baixo são colocados no setup para que os blocos do loop funcionem.

### 1.1. Bloco “Robot Library”

Este bloco tem de estar presente em todos os programas feitos no nível medio (Middle) para configurar a biblioteca.

### 1.2. Blocos “Speed Configuration”

Este bloco vai definir a velocidade de 0 a 255 que o robô vai andar.

## 2. Blocos dos loop

Como os blocos no steup, vamos passar para o loop aqui conforme montar os blocos vai desenvolvendo o programa que o robô vais desempenhar.

### 2.1. Bloco “Timing”

Ao colocar o bloco “Timing” vai temporizar os segundos que colocar no bloco a frente antes de passar para o próximo bloco.

### 2.2. Bloco “stop before obstacle”

Com este bloco o robô vai andar até que fique a distância igual que indicada a frente deste bloco. Quando estiver a essa distância o robô para, esperando por uma nova instrução.

### 2.3. Blocos “Stop the 2 Wheels”, “Lesft Wheel Stop” e o “Right Wheel Stop”

Os três blocos fazem com que as rodas parem. O bloco “Stop the 2 Wheels” faz parar as duas rodas ao mesmo tempo. O bloco “Lesft Wheels Stop” faz parar só a roda esquerda e o bloco “Right Wheels Stop” faz parar só a roda direita.

### 2.4. Blocos “Left Wheel Advances” e “Right Wheel Advances”

Os dois blocos fazem com que o robô possa andar para frente. O bloco “Left Wheel Advances” faz com que a roda ande para a frente e o bloco “Right Wheel Advances” faz o mesmo só que com a roda direita.

### 2.5. Blocos “Left Wheel Recedes” e “Right Wheel Recedes”

Os dois blocos fazem com que o robô recue. O bloco “Left Wheel Advances” faz com que a roda ande para a trás e o bloco “Right Wheel Advances” faz o mesmo só que com a roda direita.

## 3. Exemplo de programas

## 3.1. Andar em frente durante 10 segundos

## No programa em baixo no Setup:

- Bloco “Robot Lbrary” chama a biblioteca;
- Bloco “Speed Configuration” define a velocidade que vai andar o robô;

## No loop:

- Bloco “Left Wheel Advances” aciona a roda esquerda a andar para a frente;
- Bloco “Right Wheel Advances” aciona a roda direita a andar para a frente;
- Bloco “Timing” temporiza as rodas a andar para a frente durante 10 segundos;
- Bloco “Stoo the 2 Wheels” desliga as duas rodas;
- Bloco “Run Once” faz com que o programa só corra uma vez.


Durante 10 segundos

## 3.2. Andar a roda

## No programa em baixo no Setup:

- Bloco “Robot Lbrary” chama a biblioteca
- Bloco “Speed Configuration” define a velocidade que vai andar o robô

## No Loop:

- Bloco “Right Wheel Advances” aciona a roda direita a andar para a frente;
- Bloco “Left Wheel Recedes” aciona a roda esquerda do robâ a recuar;

Fazendo com que o robô roda para a esquerda sem parar


Nível Médio – iModBot@ipleiria.pt Página 1 de 7

Politécnico de Leiria 2019/2020

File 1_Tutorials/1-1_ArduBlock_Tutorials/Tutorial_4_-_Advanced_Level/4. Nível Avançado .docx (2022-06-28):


| Instituto de Engenharia de Sistemas e Computadores (INESC) de Coimbra Tutorial – Nível Avançado

Programar por blocos


Alunos:

Abel Teixeira - 2180522

Samuel Lourenço - 2180356

Docente: Luís Conde

Carlos Neves

Ano letivo: 2019/2020

# Nível Avançado (Adanced)

No nível avançado já é como se estivesse a programar. Os blocos vermelhos não necessitam de biblioteca são funções que sé usam na linguagem C++ e os blocos roxos são da biblioteca robot, está biblioteca facilitara a programação do robô.

## 1. Blocos do Setup

### 1.1. Bloco “#include < iModBot.h>”

Este bloco chama a biblioteca iModBot.h que é necessário para que os outros blocos vermelhos funcionem e também define o nome robot para os vários blocos vermelhos que iniciam com o nome “robot.”

### 1.2. Bloco “robot.ediSensorPin(S1, S2, S3, S4, S5, CLP, Near);”

Este bloco define os pinos da placa IR 74HC14. Os pinos S1, S2, S3 e S4 são dos pinos dos sensores de infravermelhos, o pino CLP corresponde ao fim-decurso da placa e o Near corresponde ao sensor infravermelho que esta a frente da placa.


### 1.3. Bloco “robot.editUltrasonicPin(trig pin, echo pin);”

Este bloco define os pinos que estão ligados ao sensor ultrassom (HC-SR04).

### 1.4. Bloco “robot.editWheelPin(Left , Right);”

Este bloco define os pinos que estão ligados aos encodares. Left ao encodar da roda esquerda e Right ao encodar da roda direita.

### 1.5. Bloco “robot.editMotorPin(INT1, INT2, INT3, INT4);”

Este bloco define os pinos que estão ligados no modulo (L293D) que controla os motores que estão acopladas as rodas do robô.

### 1.6. Bloco “robot.begin();”

Este bloco é necessário para iniciar a biblioteca e a configuração dos pinos.

## 2. Blocos dos loop

#### 2.1. Blocos “robot.getLeftEncoderCount();” e “robot.getRightEncoderCount();”

O bloco “robot.getLeftEncoderCount();” corresponde ao encoder do lado esquerdo e o “robot.getRightEncoderCount();” corresponde ao encoder do lado direito. Guardando o valor na variável com o “Nome” que colocar no bloco branco.

#### 2.2. Bloco “robot.clearEncoderCount();”

Este bloco serve para colocar os valores guardados pelos encodeares das duas rodas a zero.

#### 2.3. Bloco “robot.distance();”

Este bloco verifica a distância e guardada na variável com o nome que colocar no bloco branco.

#### 2.4. Blocos “robot.forward();” e “robot.reverse();”

O bloco “robot.forward();” faz com que o robô ande para frente e o bloco “robot.reverse();” faz com que o robô recue. Há frente de cada bloco tem de escolher a velocidade que vai andar de 0 a 255

#### 2.5. Bloco “robot.leftWheel();” e “robot.rightWheel();”

Estes blocos controlam as rodas. O bloco “robot.leftWheel();” controla a roda esquerda e o bloco “robot.rightWheel();” controla a direita. A frente de cada bloco coloca a velocidade de -255 a 255, sendo que se for um número negativo a roda respetiva recua e se for positiva ele avança.

#### 2.6. Blocos “robot.rotateLeft();” e “robot.rotateRight();”

O bloco “robot. rotateLeft ();” faz rodar para a esquerda a velocidade determinada pelo Dutty-Cycle(Modelação de Largura de Pulso) inserido. O bloco “robot. rotateRight ();” faz rodar para a direita a velocidade determinada pelo Dutty-Cycle inserido.

  2.7. Blocos “robot.turnLeft(degrees);” e “robot.turnRight(degrees);”

O bloco “robot. turnLeft ();” faz rodar o robô para a esquerda a os graus inserido. O bloco “robot. turnRight ();” faz rodar o robô para a direita a os graus inserido.

  2.8. Bloco “robot.stopMotors();”

Este bloco faz com que o robô pare ambos os motores.

#### 2.9. Bloco “robot.setSpeeds(Fast, Average, Slow)”

Este bloco serve para definir a velocidade máxima, media e mínima entre 255 a 1 que o robô vai andar.

#### 2.10. Bloco “robot.steerLeft(byte);” e “robot.steerRight(byte);”

O bloco “robot. steerLeft();” fazer com que o robô ande para a esquerda e o bloco “robot. steerRight ();” fazer com que o robô vira para a direita. Há frente de cada bloco tem de escolher a velocidade que vai andar de 0 a 255.

### 2.11. Blocos da condução autónoma

#### 2.11.1. Bloco “robot.autoDrive(byte);”

Este bloco serve para iniciar a condução automática, sem ele os blocos deste documento que começam por 2.11.x não funcionam. Ele pode enviar e receber valore.

Os valores devolvidos para a variável “Nome” têm os seguintes significados:

- 0 - Nada a reportar;
- 1 - Múltiplas linhas encontradas;
- 2 - Obstáculo encontrado;
- 3 – Não foram encontradas linhas

Os valores que colocar a frente “byte_sent” que podem ser enviados são:

- 1- Rodar para a direita;
- 2 – Rodar para a esquerda;
- 3 – Seguir em frete;
- 4 – Retroceder.

#### 2.11.2. Bloco “robot.readCLP();”

Este bloco faz a leitura do fim de curso CLP da placa IR 74HC14. Devolvendo 0 ou 1 para a variável “Nome”.

#### 2.11.3. Bloco “robot.readNear();”

Este bloco faz a leitura do infravermelho que se localiza á frente do robô da placa IR 74HC14. Devolvendo 0 ou 1 para a variável “Nome”.

#### 2.11.4. Bloco “robot.readS1();”

Este bloco faz a leitura do sensor mais à direita da placa IR 74HC14. Devolvendo 0 ou 1 para a variável “Nome”.

#### 2.11.5. Bloco “robot.readS2();”

Este bloco faz a leitura do sensor à direita da placa IR 74HC14. Devolvendo 0 ou 1 para a variável “Nome”.

#### 2.11.6. Bloco “robot.reaS3();”

Este bloco faz a leitura do sensor meio da placa IR 74HC14. Devolvendo 0 ou 1 para a variável “Nome”.

#### 2.11.7. Bloco “robot.readS4();”

Este bloco faz a leitura do sensor à esquerda da placa IR 74HC14. Devolvendo 0 ou 1 para a variável “Nome”.

#### 2.11.9. Bloco “robot.readS5();”

Este bloco faz a leitura do sensor mais a esquerda da placa IR 74HC14. Devolvendo 0 ou 1 para a variável “Nome”.

#### 2.11.10. Bloco “robot.disableCLP();”

Este bloco desabilita a leitura do sensor CLP da placa IR 74HC14 caso esteja a usar a função de condução automática proporcionada pela biblioteca.

#### 2.11.11. Bloco “robot.disableNear();”

Este bloco desabilita a leitura do sensor Near da placa IR 74HC14 caso esteja a usar a função de condução automática proporcionada pela biblioteca.

#### 2.11.12. Bloco “robot.disableUltrasonic();”

Este bloco desabilita a leitura do sensor ultrassons HC-SR04 caso esteja a usar a função de condução automática proporcionada pela biblioteca.

#### 2.11.13. Bloco “robot.endAutoDrive();”

Este bloco destinado à funcionalidade da condução autónoma e necessita de ser chamada uma vez para desassociar as interrupções previamente configuradas.

#### 2.11.14. Bloco “robot.noLineDelay(uint);”

Este bloco serve para especificar o tempo (em milissegundos) que o robô aguarda para parar os motores após ter identificado que nenhum dos sensores detetou uma linha.

## 2.12. Blocos “robot.forwardRPS(float);”, “robot.reverseRPS(float);”, “robot.rotateRightRPS(float);” e “robot. rotateLeftRPS(float);”

Estes blocos vão colocar o robô a velocidade de rotações por segundo que coloca à frente do bloco pretendido. O bloco “robot.forwardRPS(float);” faz com que as duas rodas ande para a frente a velocidade que colocar e o bloco “robot.reverseRPS(float);” faz a mesma coisa só que anda para trás. O bloco “robot.rotateRightRPS(float);” e colhe a velocidade da roda direita e o bloco “robot. rotateLeftRPS(float);” da roda esquerda.

## 2.13. Blocos “robot.forwardRPM(float);”, “robot.reverseRPM(float);”, “robot.rotateRightRPM(float);” e “robot. rotateLeftRPM(float);”

Estes blocos vão colocar o robô a velocidade de rotações por minutos que coloca à frente do bloco pretendido. O bloco “robot.forwardRPM(float);” faz com que as duas rodas ande para a frente a velocidade que colocar e o bloco “robot.reverseRPM(float);” faz a mesma coisa só que anda para trás. O bloco “robot.rotateRightRPM(float);” e colhe a velocidade da roda direita e o bloco “robot. rotateLeftRPM(float);” da roda esquerda.

## 2.14. Blocos “robot.forwardMS(float);”, “robot.reverseMS(float);”, “robot.rotateRightMS(float);” e “robot. rotateLeftMS(float);”

Estes blocos vão colocar o robô a velocidade de metros por segundo que coloca à frente do bloco pretendido. O bloco “robot.forwardMS(float);” faz com que as duas rodas ande para a frente a velocidade que colocar e o bloco “robot.reverseMS(float);” faz a mesma coisa só que anda para trás. O bloco “robot.rotateRightMS(float);” e colhe a velocidade da roda direita e o bloco “robot. rotateLeftMS(float);” da roda esquerda.

## 2.15. Bloco “robot.enSpeedAdj();”,

Esse bloco serve para ativar uma funcionalidade na biblioteca, para calcular a velocidade nas diferentes medidas RPS, RPM e MS. Sem este bloco os blocos que terminam em RPS, RPM e MS não funcionam.

## 2.16. Blocos “robot.getRightRPS();” e “robot. gerLeftRPS();”

Estes blocos guardam o valor de rotações por segundo na variável “Nome” que pode ser alterado. O bloco “robot.getRightRPS();” guarda o valor da roda direita e o “robot. gerLeftRPS();” da roda esquerda.

## 2.17. Blocos “robot.getRightRPM();” e “robot. getLeftRPM();”

Estes blocos guardam o valor de rotações por segundo na variável “Nome” que pode ser alterado. O bloco “robot.getRightRPM();” guarda o valor da roda direita e o “robot. gerLeftRPM();” da roda esquerda.

## 2.18. Blocos “robot.getRightMS();” e “robot. getLeftMS();”

Estes blocos guardam o valor de rotações por segundo na variável “Nome” que pode ser alterado. O bloco “robot.getRightMS();” guarda o valor da roda direita e o “robot. gerLeftMS();” da roda esquerda.

## 2.19. Funções também muito utilizadas na programação

Pode investigar as várias abas e descobri novas funções que possa adaptar no seu programa.

Quando se sentir já preparado passa para o Arduíno IDE sem o Ardublok e comece a programar linha a linha.


https://www.arduino.cc/reference/en/language/structure/control-structure/dowhile/

https://www.arduino.cc/reference/en/language/structure/control-structure/while/

https://www.arduino.cc/reference/en/language/structure/control-structure/else/

https://www.arduino.cc/reference/pt/language/structure/control-structure/if/

3. Exemplo de um programa
  3.1. Robô vai andar em frente

No programa em baixo no Setup:

Bloco “#include <iModBot.h>” chama a biblioteca;

Bloco “robot.editMotorPin(INT1, INT2, INT3, INT4);” de define os pinos que vão controlar as rodas;

Bloco “robot.begin();” configura a biblioteca e os pinos;

No loop:

Bloco “robot.forward();” faz com que o robô ande para a frente.


Nível Avançada – iModBot@ipleiria.pt Página 1 de 7

Politécnico de Leiria 2019/2020

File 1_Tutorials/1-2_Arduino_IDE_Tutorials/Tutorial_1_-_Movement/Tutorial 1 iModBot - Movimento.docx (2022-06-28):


| Tutorial – Movimento iModBot@ipleiria.pt

# Introdução

O robô EDURobot é um veículo elétrico de pequenas proporções controlado pelo microcontrolador ESP32. Este microcontrolador pode ser programado usando a linguagem C/C++ e o software gratuito Arduino IDE.

Este tutorial vai focar-se no movimento do robô.

O robô possui duas rodas que lhe permitem mover em qualquer direção. Cada roda possui um motor elétrico cuja direção é controlada pela sua polarização.

Este motor é conectado ao módulo L293D como descrito no guia de montagem:


O controlo dos motores é efetuado diretamente pelo circuito integrado L293D, sendo este controlado pelo microcontrolador ESP32. A velocidade de cada roda é controlada por modulação de largura de pulso.

São usados dois pinos para controlar cada motor, sendo assim usados quatro pinos no total para o controlo das duas rodas.
Estes quatro pinos, geralmente, podem ser qualquer GPIO (General Purpose Input output). Cada módulo de desenvolvimento baseado no microcontrolador ESP32 possui pinos (GPIO) restritos e pinos disponíveis diferentes.

O módulo que é enviado juntamente com o kit EDURobot é denominado “DOIT ESP32 DevKit V1”. Se for usada a biblioteca “RobotOnLine” por defeito os pinos destinados ao controlo das rodas serão:

- GPIO 4 e GPIO 16, para a roda direita;
- GPIO 17 e GPIO 18, para a roda esquerda.

Número do GPIO: | Estado lógico: | Efeito:
4 | 1 | Motor direito recua.
16 | 0
4 | 0 | Motor direito avança.
16 | 1
17 | 1 | Motor esquerdo avança.
18 | 0
17 | 0 | Motor esquerdo recua.
18 | 1

Usando as funções proporcionadas pelo ambiente Arduino um estado lógico “1” pode ser causado no pino “4” usando “digitalWrite(4, HIGH);”, da mesma maneira um estado lógico “0” pode ser causado usando “digitalWrite(4, LOW);”.

Para parar um motor é necessário colocar ambos os pinos no estado lógico “0”.

Para poder controlar a velocidade a que o motor gira é apenas necessário substituir o estado lógico “1”, indicado na tabela acima, por um sinal PWM.

A biblioteca “RobotOnLine” usa, por defeito, os seguintes parametros para o sinal PWM:

- Frequência de 5kHz.
- Resolução de 8 bits.

## Ex 1 - Controlo do movimento simples.

#### Descrição

Este exemplo permite mover o robô em qualquer direção sem controlo da velocidade.

#### Sintaxe

digitalWrite(pino, estado);

#### Parâmetros

pino //número associado ao pino

estado //HIGH ou LOW

#### Respostas

Nenhum

### Exemplo:

void setup()

{

pinMode( 4,OUTPUT); //Direita

pinMode(16,OUTPUT); //Direita

pinMode(17,OUTPUT); //Esquerda

pinMode(18,OUTPUT); //Esquerda

}

void loop()

{

// Para seguir em frente

digitalWrite( 4, LOW);

digitalWrite(16, HIGH);

digitalWrite(17, HIGH);

digitalWrite(18, LOW);

delay(1000);

// Para recuar

digitalWrite( 4, HIGH);

digitalWrite(16, LOW);

digitalWrite(17, LOW);

digitalWrite(18, HIGH);

delay(1000);

// Rodar para a direita

digitalWrite( 4, HIGH);

digitalWrite(16, LOW);

digitalWrite(17, HIGH);

digitalWrite(18, LOW);

delay(1000);

// Rodar para a esquerda

digitalWrite( 4, LOW);

digitalWrite(16, HIGH);

digitalWrite(17, LOW);

digitalWrite(18, HIGH);

delay(1000);

//Parar os motores

digitalWrite( 4, LOW);

digitalWrite(16, LOW);

digitalWrite(17, LOW);

digitalWrite(18, LOW);

delay(1000);

}

Ex 2 - Controlo usando a biblioteca
Descrição Permite controlar o movimento do robô em qualquer direção e também o controlo da velocidade das rodas. Sintaxe forward( velocidade ); reverse(velocidade); rotateLeft(velocidade); rotateRight(velocidade): stopMotors(); Parâmetros Velocidade = é um numero de 0 a 255. Respostas O número de bytes disponíveis para serem lidos | Exemplo: #include <robotOnLine.h> robotOnLine robot; void setup() { robot.begin(); } void loop() { // Velocidade // Pode variar de 1 a 255 byte speed = 255; // Para seguir em frente robot.forward(speed); delay(500); // Para recuar robot.reverse(speed); delay(500); // Rodar para a direita robot.rotateRight(speed); delay(500); // Rodar para a esquerda robot.rotateLeft(speed); delay(500); // Parar os motores robot.stopMotors(); delay(1000); }

## Ex 3 - Controlo individual de cada roda usando a biblioteca

Descrição Neste exemplo é possível controlar individualmente a direção de cada roda. Sintaxe rightWheel( velocidade ); leftWheel( velocidade ); Parâmetros - Velocidade = número de -255 a 255, um valor negativo faz a roda recuar e vice-versa. Um 0 faz a roda parar. Respostas Nada | Exemplo: #include <robotOnLine.h> robotOnLine robot; void setup() { robot.begin(); } void loop() { // Mover roda esquerda em frente robot.leftWheel(255); delay(1000); // Mover roda esquerda para trás robot.leftWheel(-255); delay(1000); // Mover roda direita em frente robot.rightWheel(255); delay(1000); // Mover roda direita para trás robot.rightWheel(-255); delay(1000); }

## Ex 4 - Rodar o robô “n” degraus usando a biblioteca

Descrição Neste exemplo é possível rodar o robô “n” graus e escolher para que lado o mesmo deve rodar (esquerda ou direita). Sintaxe turnLeft( graus ); turnRight( graus ); Parâmetros - Graus = é um número de 1 a 360 que corresponde a quantos graus o robô irá rodar. Um 0 faz o robô rodar 90 graus. Respostas Nada | Exemplo: #include <robotOnLine.h> robotOnLine robot; void setup() { robot.begin(); } void loop() { // Rodar para a esquerda 90 graus robot.turnLeft(90); delay(1000); // Rodar para a direita 270 graus robot.rightWheel(270); delay(1000); }

## Ex 5 - Controlar velocidade e movimento sem biblioteca

#### Descrição

Este exemplo permite controlar o movimento do robô sem recurso à biblioteca “RobotOnLine”.

#### Sintaxe

ledcSetup(canalPWM, frequenciaPWM, resoluçãoPWM);

ledcWrite(canalPWM, PWM);

#### Parâmetros

canalPWM = canal PWM de 0 a 15.

frequenciaPWM = frequência de 1 Hz a 312.5kHz

resoluçãoPWM = resolução do pulso PWM

PWM = largura do pulso PWM (8 bits, 0 a 255 neste caso)

#### Returns

#### Exemplo:

#define PWM_Frequency 5000 // PWM frequency, up to 312.5kHz

#define _IN1_PWM_channel 0 // select the channel number

#define _IN2_PWM_channel 1 // there are 15 channels,

#define _IN3_PWM_channel 2 // choose between 0 to 15

#define _IN4_PWM_channel 3 // (not related to the pins)

#define PWM_RESOUTION 8 // 8 bits

//motor pins IN1&IN2 right engine

byte _IN1 = 4; //IO15 and 5 are HIGH during boot.

byte _IN2 = 16;

//IN3&IN4 left engine

byte _IN3 = 17;

byte _IN4 = 18;

void setup()

{

pinMode(4,OUTPUT);

pinMode(16,OUTPUT);

pinMode(17,OUTPUT);

pinMode(18,OUTPUT);

//setup PWM for motor pins

ledcSetup(_IN1_PWM_channel, PWM_Frequency, PWM_RESOUTION);

ledcAttachPin(_IN1, _IN1_PWM_channel);

ledcSetup(_IN2_PWM_channel, PWM_Frequency, PWM_RESOUTION);

ledcAttachPin(_IN2, _IN2_PWM_channel);

ledcSetup(_IN3_PWM_channel, PWM_Frequency, PWM_RESOUTION);

ledcAttachPin(_IN3, _IN3_PWM_channel);

ledcSetup(_IN4_PWM_channel, PWM_Frequency, PWM_RESOUTION);

ledcAttachPin(_IN4, _IN4_PWM_channel);

ledcWrite(_IN1_PWM_channel, 0);

ledcWrite(_IN2_PWM_channel, 0);

ledcWrite(_IN3_PWM_channel, 0);

ledcWrite(_IN4_PWM_channel, 0);

}

void loop()

{

byte speed = 255;

// move forward

//right engine forward

ledcWrite(_IN1_PWM_channel, 0);

ledcWrite(_IN2_PWM_channel, speed);

//left engine forward

ledcWrite(_IN3_PWM_channel, speed);

ledcWrite(_IN4_PWM_channel, 0);

delay(1000);

// turn left

//right engine forward

ledcWrite(_IN1_PWM_channel, 0);

ledcWrite(_IN2_PWM_channel, speed);

//left engine reverse

ledcWrite(_IN3_PWM_channel, 0);

ledcWrite(_IN4_PWM_channel, speed);

delay(1000);

// turn right

//right engine reverse

ledcWrite(_IN1_PWM_channel, speed);

ledcWrite(_IN2_PWM_channel, 0);

//left engine forward

ledcWrite(_IN3_PWM_channel, speed);

ledcWrite(_IN4_PWM_channel, 0);

delay(1000);

// reverse

//right engine reverse

ledcWrite(_IN1_PWM_channel, speed);

ledcWrite(_IN2_PWM_channel, 0);

//left engine reverse

ledcWrite(_IN3_PWM_channel, 0);

ledcWrite(_IN4_PWM_channel, speed);

delay(1000);

}

Tutorial – Movimento iModBot@ipleiria.pt Página 30 de 30

Politécnico de Leiria 2019/2020

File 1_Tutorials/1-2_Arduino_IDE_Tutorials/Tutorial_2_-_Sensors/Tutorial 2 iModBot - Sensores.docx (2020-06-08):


| Tutorial – Movimento iModBot@ipleiria.pt

# Introdução

O robô EDURobot é um veículo elétrico de pequenas proporções controlado pelo microcontrolador ESP32. Este microcontrolador pode ser programado usando a linguagem C/C++ e o software gratuito Arduino IDE.

Este tutorial vai focar-se na leitura dos vários sensores do robô.

O robô possui os seguintes tipos de sensores:

- Ultrassons, para detetar obstáculos distantes;
- Fim de curso, para detetar uma colisão;
- Sensores infravermelho (IR), para detetar um percurso (Linha perta desenhada numa superfície branca) e também para detetar obstáculos a curta distância;
- Encoder óticos, para obter um feedback da posição das rodas.

นาย arduino: ใช้ Arduino ติดต่อกับ Ping Ultrasonic Sensor ...

O sensor de ultrassons devolve uma distância à qual se encontra um obstáculo. Esta informação será útil para evitar que o robô colida com um obstáculo.

Ligações deste módulo:

Echo | D12
Trig | D14

Jual Produk Module Tcrt5000 5 Channel Line Murah dan Terlengkap ...

O sensor fim de curso é um botão (switch, denominado CLP) colocado na parte da frente do módulo de sensores IR.
Os dois LED emissor e recetor infravermelho, denominado sensor “Near”, acima do switch permitem detetar obstáculos a curta distância, a luz natural poderá causar leituras erradas no recetor infravermelho.

Os cinco sensores infravermelho na parte inferior da placa, denominados S1, S2 … S5, permitem detetar uma linha preta numa superfície clara (branca).

Ligações deste módulo:

S1 | D25
S2 | D33
S3 | D32
S4 | D35
S5 | D34
CLP | VN
Near | VP

Motor Speed Encoder Sensor | Open ImpulseOpen Impulse

Os sensores/encoder óticos servem para obter um feedback da rotação das rodas podendo deste modo obter a distância percorrida e saber se uma está a rodar mais rapidamente que a outra.

Ligações deste módulo:

Encoder da roda esquerda | D0 | D26
Encoder da roda direita | D0 | D27

Deve haver uma peça semelhante a esta no eixo da roda:

Photoelectric Encoder Disc For Motor Speed Measurement, मोटर ...

Esta peça permite ao Encoder fazer a contagem dos pulsos da roda. Cada vez que uma roda dá uma volta completa (360º) a contagem deve aumentar 40 pulsos.

A contagem dos pulsos aumenta sempre, independentemente da direção em que as rodas se deslocam.

O número de pulsos também pode ser usado para calcular a distância percorrida pela roda, para tal precisamos de medir o diâmetro (d) da roda. Após sabermos o diâmetro vamos calcular o perímetro (P) usando a fórmula P = π * d. Após conhecermos o perímetro sabemos que 40 pulsos equivalem ao perímetro calculado, desta forma a distância percorrida (D) pode ser calculada da seguinte maneira:

D=(pulsos * P)/40 em que P é o perímetro da roda, “pulsos” o número de pulsos contados e D a distância percorrida.

Ex1 - Usar sensor de ultrassons com a biblioteca
Descrição Este exemplo obter a distância, em cm, à qual se encontra um obstáculo e apresentar a mesma no monitor série. Sintaxe Distance(); = devolve o valor, em cm, da distancia medida. Parâmetros Nenhum Respostas Nenhum | Exemplo: #include <robotOnLine.h> robotOnLine robot; void setup() { robot.begin(); Serial.begin(115200); } void loop() { byte dist = robot.distance(); Serial.println(dist); delay(250); }

Ex2 - Ler sensor CLP, Near, S1, S2, S3, S4 e S5

#### Descrição

Este exemplo permite obter o estado de cada pino o apresentar o mesmo no monitor série.

#### Sintaxe

readCLP();

readNear();

#### readS1();

readS2();
readS3();
readS4();
readS5();

#### Parâmetros

state = variável que recebe o valor da função, 1 ou 0, consoante o estado do pino.

#### Respostas

Nenhum

Exemplo:

#include <robotOnLine.h>

robotOnLine robot;

void setup()

{

robot.begin();

Serial.begin(115200);

}

void loop()

{

bool state = 0;

state = robot.readCLP();

Serial.print("Estado do pino CLP: ");

Serial.println(state);

state = robot.readNear();

Serial.print("Estado do pino Near: ");

Serial.println(state);

state = robot.readS1();

Serial.print("Estado do pino S1: ");

Serial.println(state);

state = robot.readS2();

Serial.print("Estado do pino S2: ");

Serial.println(state);

state = robot.readS3();

Serial.print("Estado do pino S3: ");

Serial.println(state);

state = robot.readS4();

Serial.print("Estado do pino S4: ");

Serial.println(state);

state = robot.readS5();

Serial.print("Estado do pino S5: ");

Serial.println(state);

delay(250);

}

Ex3 - Ler e reiniciar a contagem de pulsos dos Encoders.
Descrição Este exemplo permite ler o número de pulsos contados pelos Encoder óticos e apresentar os mesmos no monitor série. Sintaxe getLeftEncoderCount();/* devolve um número de pulsos contados pelo Encoder da roda esquerda */ getRightEncoderCount(); /* devolve um número de pulsos contados pelo Encoder da roda direita */ clearEncoderCount(); /* coloca a contagem de pulsos a zero */ Parâmetros Nenhum Respostas “short” é um tipo de variável com metade do tamanho da variável de tipo “int” | Exemplo: #include <robotOnLine.h> robotOnLine robot; short leftPulse = 0; short rightPulse = 0; void setup() { robot.begin(); Serial.begin(115200); } void loop() { leftPulse = robot.getLeftEncoderCount(); rightPulse = robot.getRightEncoderCount(); Serial.print("Pulso da roda esquerda: "); Serial.print(leftPulse); Serial.print("\t"); Serial.print("Pulso da roda direita: "); Serial.println(rightPulse); if( (leftPulse > 10000) || (rightPulse > 10000) ) { robot.clearEncoderCount(); } delay(250); }

Tutorial – Movimento iModBot@ipleiria.pt Página 30 de 30

Politécnico de Leiria 2019/2020

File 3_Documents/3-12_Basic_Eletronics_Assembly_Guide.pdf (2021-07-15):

# Guia Básico Para Montagem de Circuitos Elétricos

Elaborado por:
Abel Teixeira – 2180522
Samuel Lourenço – 2180356

Verificado por:
Marco Pereira – 2190516
Nelson Henriques – 2190514

Orientado por:
Carlos Neves
Luís Conde

# iModBot

### ÍNDICE


V1.1 – 22/06/2021 | 1

Guia Básico Para Montagem de Circuitos Elétricos

### O que é um circuito elétrico?

Em termos simples, é um caminho fechado pelo qual circula uma corrente elétrica numa mesma direção e de forma ordenada.

Um circuito elétrico pode ser composto por vários componentes e elementos, alguns mais necessários que outros, como a fonte de tensão, a massa e os cabos. O funcionamento de determinado circuito vai depender em grande medida dos
componentes a utilizar.

A montagem dos circuitos vai ser numa breadboard, conhecida também por outros nomes como protoboard ou placa de ensaios. A placa tem pequenos furos ou orifícios os quais estão ligados entre si por conexões condutoras. É um componente bastante simples de usar e que permite-nos montar e desmontar uma ampliada diversidade de circuitos com facilidade.

É importante conhecer e perceber a direção na qual os componentes devem ser ligados porque caso contrário arriscamo-nos a cometer erros que vão impedir que o circuito funcione como deve ser. Os cabos condutores, que bem podem ser de cobre, fósforo ou estanho, vão estar distribuídos basicamente da seguinte maneira, segundo o padrão típico duma protoboard como a antes indicada. As linhas verticais são chamadas de buses na breadboard e vão representar o positivo e o negativo, que em geral, se o utilizador o achar conveniente, ao positivo como a fonte de tensão e ao negativo como massa ou terra. As linhas horizontais são o campo onde vamos fazer as ligações dos circuitos e funcionam basicamente da seguinte maneira: uma linha horizontal representa o mesmo nó, pelo qual se juntarmos dois fios no mesmo ponto da linha, vai significar que estão ligados entre si. Se fizermos ao contrário, é dizer, ligar um fio num ponto da horizontal e outro numa linha horizontal diferente, estes não vão estar ligados entre si.

Figura 1 - Breadboard típica


V1.1 – 22/06/2021 | 2

Circuitos Elétricos

Figura 2 - Configuração da breadboard

Uma sugestão ao momento de armar o circuito seria fazê-lo de forma organizada, com fios pequenos, evitando fiação aérea pois fica mais confuso de perceber em circuitos mais complexos.

### Circuitos Elétricos Básicos

- Ligação em Série

Uma ligação em série basicamente segue um mesmo caminho para a passagem de corrente. No seguinte exemplo temos três resistências ligadas em serie com uma fonte de tensão. As setas representam a corrente que percorre um único caminho.

Cada um dos números apresentados na imagem a seguir, representa uma linha de pontos como está apresentado na Figura 4, assim fazemos uma ligação em serie.


V1.1 – 22/06/2021 | 3

Circuitos Elétricos

Figura 3 - Esquema de circuito em série

Figura 4 - Montagem de circuito em série na breadboard

Exemplos:
Neste caso, temos um circuito com quatro diodos led e uma resistência em serie alimentados por uma bateria.


V1.1 – 22/06/2021 | 4

Circuitos Elétricos

Figura 6 - Circuito em serie com diodos na breadboard

- Ligação em Paralelo
Uma ligação em paralelo consiste em que os componentes elétricos coincidam em cada um dos seus extremos, é dizer, a sua saída com a sua saída e a sua entrada com a sua entrada. Como podemos ver na Figura 7, partilham um ponto numa parte das três diferentes resistências, e outro ponto diferente para a outra parte das três resistências. Como podemos ver na Figura 7 estão ligadas três resistências numa mesma linha de pontos para a parte de acima do circuito e outra diferente linha de pontos para a outra parte das resistências.

Figura 7 - Esquema de circuito em paralelo

Figura 5 - Esquema de circuito em serie com diodos


V1.1 – 22/06/2021 | 5

Circuitos Elétricos

Figura 8 - Montagem de circuito em paralelo na breadboard

Exemplos:
Neste caso, temos uma ligação paralela de 3 diodos LED com 3 resistências de proteção, na primeira imagem temos o esquema e na segunda temos a ligação na breadboard, como podemos ver, partilham uma linha de pontos interligados com fios e não diretamente, mas é indiferente para a perfeita execução do circuito.

Figura 9 - Esquema de circuito em paralelo com diodos e resistências


V1.1 – 22/06/2021 | 6

Circuitos Elétricos

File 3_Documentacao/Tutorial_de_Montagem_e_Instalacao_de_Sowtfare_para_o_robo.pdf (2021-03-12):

INSTITUTO DE ENGENHARIA DE

SISTEMAS E COMPUTADORES

### (INESC) DE COIMBRA

Tutorial

# Tutorial de Montagem e Instalação de Software Para o Robô


Elaborado por:
Abel Teixeira - 2180522
Samuel Lourenço - 2180356

2019/2020

Politécnico de Leiria | 2020/2021
Tutorial - iModBot@ipleiria.pt | 1

### ÍNDICE

Tutorial - iModBot@ipleiria.pt | 1

INTRODUÇÃO

Este guia serve para orientar o utilizador nos primeiros passos do robô educacional iModBot, na sua montagem, instalação dos diferentes softwares e na programação e utilização dos mesmos. Este guia compõe vários componentes importantes do projeto iModBot: montagem e programação. Mostra também os links com os arquivos e os tutoriais necessários

### 1. Instalação de Sowtfares úteis para o robô

### 1.1 Instalação do Arduino IDE

- Carrega no link da página de arduino para descarregar o Arduino IDE. Link: https://www.arduino.cc/en/software

No quadro da direita escolhe o sistema operativo do seu computador (Figura 1).

Figura 1 - arduino.cc


Tutorial - iModBot@ipleiria.pt | 2
- Clicamos em “JUST DOWNLOAD” (Figura 2).

Figura 2 - Just Download Arduino IDE

- No Windows 10, clicamos em “Obter”, para assim fazer o download do Arduino IDE (Figura 3).

Figura 3 - Obter Arduino IDE

- No caso de Windows 10, será aberto o Microsoft Store e começará a descarga e instalação de Arduino IDE, e quando estiver pronto, clicamos em “Abrir”, como na Figura 4, e permitimos os acessos necessários para que seja aberta a janela de


Tutorial - iModBot@ipleiria.pt | 3

Arduino, e já teremos o Arduino IDE pronto para programar, ao momento de abrir devemos ter uma janela igual à Figura 5.

Figura 4 - Iniciar Arduino


Tutorial - iModBot@ipleiria.pt | 4

Figura 5 - Arduino IDE Instalado

O site também possui guias de instalação passo a passo para cada sistema operativo. Guias de instalação:
- Windows: https://www.arduino.cc/en/Guide/Windows
- Linux: https://www.arduino.cc/en/Guide/Linux
- Mac Os X: https://www.arduino.cc/en/Guide/MacOSX
- Versão portátil (Windows e Linux): https://www.arduino.cc/en/Guide/PortableIDE
- ChromeOs: https://chrome.google.com/webstore/detail/arduino-create/dcgicpihgkmccjigalccipmjlnjopdfe (particulares) e https://create.arduino.cc/plans/chrome-app (educativo)

Tutorial - iModBot@ipleiria.pt | 5

### 1.2 Instalação de bibliotecas para Arduino com funções para o robô

O software Arduino IDE precisa mais bibliotecas para efetuar funções especificamente criadas para o robô, por isso, é necessário fazer as seguintes alterações do programa.
- Carrega no link apresentado a seguir e descarrega o arquivo comprimido “libraries.7z”, como é apresentado na Figura 6.

Figura 6 - Descarregar libraries.7z

- Após o download, descomprima o arquivo até ter uma pasta “libraries”. Abrir a pasta para verificar que se encontram todas as pastas mostradas na Figura 7.

Figura 7 - Bibliotecas do Arduino

Tutorial - iModBot@ipleiria.pt | 6
- Copiamos a pasta “libraries”, localizada, geralmente, no endereço mostrado na Figura 8.

Figura 8 - Copiar Libraries

- E colamos na pasta “Arduino”, que foi criada automaticamente no momento da instalação do Arduino IDE, geralmente localizada no endereço que é mostrado na Figura 9. Geralmente ao instalar, esta pasta vem vazia por defeito, mas, caso já tenha uma pasta com nome “libraries”, basta substituí-la por a pasta “libraries” que descarregou.

Figura 9 - Colar libraries


Tutorial - iModBot@ipleiria.pt | 7
- Para verificar que já temos instaladas as bibliotecas que precisamos, vamos abrir o Arduíno IDE para colocar exemplos de programação do nosso robô, que se encontra nas bibliotecas agora instaladas. Seguimos os comandos mostrados na Figura 10, e caso apareçam as opções que estão assinaladas na Figura 10, é porque fizemos corretamente a instalação das bibliotecas para o robô.

Figura 10 - Arduino com bibliotecas instaladas

### 1.3 Configuração do Arduino IDE para programar o ESP32

Passo muito importante para programar o nosso robô. No momento de instalar o Arduino não é possível programar a placa ESP32, por isso, é necessário fazer configurações importantes dentro do Arduino IDE para começar a programar o ESP32.
Para isso, devemos seguir os seguintes passos.
- No Arduíno IDE, no separador “Ficheiro”, clicamos em “Preferências” (Figura 11).


Tutorial - iModBot@ipleiria.pt | 8

Figura 11 - Ficheiro > Preferências

- Irá aparecer uma nova janela igual à da Figura 12, onde vamos clicar no ícone igual ao assinalado na Figura 12.

Figura 12 - "Janela Preferências"

- Nesta nova janela que aparecerá ao fazer o passo anterior iremos colar no espaço vazio (Figura 13) o link “https://dl.espressif.com/dl/package_esp32_index.json”, e deverá ficar como na Figura 14 e clicar em “OK”.


Tutorial - iModBot@ipleiria.pt | 9

Figura 13 – Adicionar gestor de placas

Figura 14 - Link colado

- Voltará à janela “Preferências”, mas com o link que colámos na parte “URL Adicionais do Gestor de Placas”, e clicamos em “OK” (Figura 15).

Figura 15 - Janela Preferências configurada


Tutorial - iModBot@ipleiria.pt | 10
- A seguir, clicamos em “Ferramentas”, depois em “Placa” e finalmente em “Gestor de Placas” como pode-se ver na Figura 16.

Figura 16 – Gestor de placas

- Na janela que aparece na Figura 17, no espaço em branco assinalado escrevemos “ESP32”, seguidamente quando aparecer a opção que é mostrada na Figura 18 procuramos a versão mais recente e seguidamente clicamos em “Instalar”, como é mostrado na Figura 18 e iniciará a instalação para poder programar a placa ESP32 com Arduíno IDE.

Figura 17 – Gestor de placas


Tutorial - iModBot@ipleiria.pt | 11

Figura 18 – Seleção da placa

- Verificamos que ficou instalado e clicamos em fechar (Figura 19).

Figura 19 – Seleção da placa

- Por último seguimos o caminho de comandos mostrados na Figura 20 que são, “Ferramentas”, seguido de “Placa”, seguido de “ESP32 Arduíno” e finalizamos em “ESP32 Dev Module”. E já temos o Arduíno IDE configurado para programar a placa ESP32 que funciona como o cérebro do robô.


Tutorial - iModBot@ipleiria.pt | 12

Figura 20

- O link que vamos disponibilizar é um vídeo que resume os passos caso exista alguma dúvida no processo.

Link: https://www.youtube.com/watch?v=xiqXJj58ynI&ab_channel=SamuelLouren%C3%A7o

Tutorial - iModBot@ipleiria.pt | 13

### 1.4 Instalação de Ardublocks no Arduino IDE

Para programar facilmente o robô vamos utilizar uma ferramenta chamada “Ardublocks”, que permite programar funções no robô com a simples ação de colocar blocos com uma ordem específica que fará uma ação, ou conjunto de ações, programadas para o robô. Para instalar isso é preciso seguir os seguintes passos.
- Na pasta “ArduBlock” descarregue o ficheiro “ardublock-beta-20200614.jar” (Figura 21).

Figura 21 - Descarregar ficheiro

- No Arduíno IDE, em Ficheiro, clicamos em “Preferências” (Figura 22).

Figura 22 - Preferências

- Procuramos o endereço mostrado na Figura 23 nas pastas do seu computador até chegar à pasta como na Figura 24.


Tutorial - iModBot@ipleiria.pt | 14

Figura 23 – Procurar o endereço

Figura 24 - Endereço

- Neste endereço criamos uma pasta com o nome “tools” (Figura 25) e nesta nova pasta criamos uma pasta com o nome “ArduBlockTool” (Figura 26) e nesta pasta criamos mais uma pasta com o nome “tool” (Figura 27).


Tutorial - iModBot@ipleiria.pt | 15

Figura 25 – Criação da pasta

Figura 26 – Pasta ArdublockTool

Tutorial - iModBot@ipleiria.pt | 16

Figura 27 – Pasta tool

- E dentro desta última pasta (Figura 27), vamos colar o arquivo descarregado no primeiro passo (Figura 21).

Figura 28 – Arquivo Ardublock


Tutorial - iModBot@ipleiria.pt | 17
- E pronto, no Arduíno IDE deverá aparecer em “Ferramentas” uma opção chamada “ArduBlock” como na Figura 29. Que ao clicar abrirá uma nova janela igual à da Figura 30, e o Arduíno IDE está pronto para programar o robô!

Figura 29 - Ardublock

Figura 30 – Ambiente do Ardublock


Tutorial - iModBot@ipleiria.pt | 18

### 2. Montagem do iModBot

### 2.1 Componentes

Está disponível uma lista com todos os componentes, com uma sugestão ou referencia de onde e a que preço pode o utilizador adquiri-los com varia opção de preços. Também se encontra uma listagem descritiva dos componentes para ajudar a utilizar e perceber melhor o seu funcionamento. É muito importante ter todos os componentes tal como a listagem a seguir. No próximo link descarrega o ficheiro Excel chamado “Listagem de componentes iModBot + links de compra auxiliares” onde conseguirá alguns links de compra seguido da listagem completa dos componentes eletrónicos. Link:https://github.com/BelenEJS/iModBot/tree/main/Tutorial%20de%20montagem%20iMod Bot

Figura 31 – Listagem de componentes

A seguir alguns dos componentes que vamos encontrar na listagem de compras, no ponto 2.3 será explicado o funcionamento de cada um dos aparelhos eletrónicos.

Tutorial - iModBot@ipleiria.pt | 19
- DOIT ESP32 DevKit V1 – módulo que será responsável pelas comunicações e controlo.

Figura 32 - Placa ESP32

- Módulo de controlo dos motores, L293D

Figura 33 - L293D

- Placa de sensores IR 74HC14

Figura 34 - Placa de sensores

Tutorial - iModBot@ipleiria.pt | 20
- Encoder Óticos

Figura 35 - Encoder Ótico

- HC-SR04

Figura 36 - HC-SR04

- Módulo de carga TP4056

Figura 37 - TP4056

- Módulo elevador de tensão MT3608

Figura 38 - Módulo elevador de tensão MT3608

Tutorial - iModBot@ipleiria.pt | 21
- Bateria de lítio de iões, 3.7v, 2500mAh

Figura 39 - Batería

### 2.2 Ligações e montagem

Estabeleça as ligações como demonstrado nas imagens seguintes. Também está disponível um vídeo que demonstra a montagem dos vários componentes.
O robô deve ficar com o seguinte aspeto, mas no início quando o utilizador estiver a começar a interagir com o dispositivo pode ir montando tudo numa breadboard de forma organizada e otimizando o espeço, pois, o robô deve ser especialmente pequeno e deve entrar na estrutura base com as rodas que se indica abaixo. Se o utilizador é iniciante na área de circuitos e eletrónica, sugerimos ler o tutorial de circuitos elétricos e montagem básica de circuitos, na pasta Tutorial de montagem iModBot.
Link de guia básico de montagem de circuitos elétricos para iniciantes: https://github.com/BelenEJS/iModBot


Tutorial - iModBot@ipleiria.pt | 22

Figura 40 - Robô montado

Siga os passos do vídeo para ter o robô pronto a fazer as tarefas que proponha, caso não ficar esclarecido com o vídeo de como efetuar as ligações dos componentes eletrónicos siga os passos referidos no ponto 2.3.
Link do vídeo:
https://www.youtube.com/watch?v=i4wFh0GqzkM&feature=emb_logo&ab_channel=AbTx

### 2.3 Passos a seguir

Passo 1: Ligamos o módulo elevador de tensão MT3608 ao modulo de carga TP4056 e este à bateria de lítio. Para ligar os dois módulos, devemos ligar o pin Vin+ do modulo elevador de tensão ao out+ do modulo de carga, e assim também o vin- do elevador de tensão ao out-. Depois para ligar a bateria, ligamos o pin B+ ao positivo da bateria ou fio vermelho e o pin B- ao negativo da bateria ou fio preto.


Tutorial - iModBot@ipleiria.pt | 23

Figura 41 - Passo 1

Passo 2: ligar o pin VIN+ do módulo elevador de tensão ao ESP32 e ao módulo de controlo dos motores como se mostra na Figura 42. Depois ligamos o pin VOUT- ao modulo de controlo dos motores.


Tutorial - iModBot@ipleiria.pt | 24

Figura 42 - Passo 2

Passo 3: ligação dos motores ao módulo de controlo dos motores assim como se mostra na Figura 43. Estes vão controlar o movimento das rodas direita e esquerda.

Figura 43 - Passo 3

Passo 4: deve ligar o ESP32 ao módulo de controlo dos motores nos pinos indicados com as cores seguintes.


Tutorial - iModBot@ipleiria.pt | 25

Figura 44 - Passo 4


Tutorial - iModBot@ipleiria.pt | 26

Passo 5: Para alimentar o sensor de proximidade, é preciso fazer as seguintes ligações.

Figura 45 - Passo 5

Passo 6: Agora, temos de ligar os pinos do ESP32 ao sensor de proximidade, mas, primeiro devemos passar pelo canal Bidirecional conversor de deslocador de nível lógico.

Figura 46 - Passo 6


Tutorial - iModBot@ipleiria.pt | 27

Passo 7: Neste passo, vamos alimentar a placa de sensores infravermelhos que servem para detetar cor preto e cores claras e os dois sensores infravermelhos que servem para receber a velocidade das rodas.

Figura 47 - Passo 7

Passo 8: Agora, vamos ligar dois pinos do ESP32 aos respetivos sensores infravermelhos de velocidade, é importante ter em conta a roda direita e esquerda, para quando programar o robô não existir erros, porque as vezes a roda direita não vai ter a mesma velocidade do que a esquerda ou ao contrário, para fazer curvas, rodar em círculos, etc.

Tutorial - iModBot@ipleiria.pt | 28

Figura 48 - Passo 8

Passo 9: E por último, vamos ligar com cabos macho-fêmea, a placa ESP32 para a placa de sensores infravermelhos, ter em conta as cores para não ligar erradamente, só assim fazemos com que o robô possa seguir linhas pretas ou mais funções.

Figura 49 - Passo 9


Tutorial - iModBot@ipleiria.pt | 29

### 2.4 Programar o teu robô

Nesta altura, já tens o teu próprio robô montado e os softwares prontos para programar o robô, e para verificar os movimentos do robô, a ligação ao WiFi e os sensores corretamente ligados, vamos começar pelas funções básicas que se encontram na ferramenta “ArduBlocks”.
Para isso, primeiro devemos ligar, com ajuda de um cabo USB, o teu computador à placa ESP32 (referida na Figura 32) e abrimos o Arduíno IDE e neste software a ferramenta ArduBlocks (referida na Figura 29).
Na Figura 49 vê-se a página principal do ArduBlocks, na parte esquerda encontram-se o resto dos blocos úteis para o funcionamento do nosso robô.

Figura 50 - ArduBlocks aberto

### 2.5 Piscar LED e ligar WiFi

Na parte esquerda, vamos começar por blocos de nível iniciante e vamos clicar em “Beginner RBC_IPL” e movimentamos o bloco “Flashing Led” que fará piscar um LED da placa ESP32, no bloco “Robô OTA”, que é o bloco que usaremos nas tarefas de nível iniciante, existem dois blocos na parte “ssid” e “password” onde em ssid colocaremos o nome da rede WiFi à que pretendemos ligar o robô, e em password escrevemos a palavra-passe daquela rede WiFi, quando estiver prontos os blocos ligados como na Figura 50, clicamos em “Upload to Arduíno”, isto faz que sejam transformados os blocos em linguagem de programação “C++”, automaticamente será enviado o código para a placa ESP32 e em instantes piscará o LED e isto garante a ligação ao WiFi.

Tutorial - iModBot@ipleiria.pt | 30

Figura 51 - Upload to Arduíno

### 2.6 Apagar Bloco

Para apagar um bloco qualquer da ferramenta “ArduBlocks” basta movimentar o bloco que queremos apagar para a parte esquerda como é mostrado na Figura 51. Neste exemplo apagamos todos os blocos que anteriormente colocamos.


Tutorial - iModBot@ipleiria.pt | 31

Figura 52 - Apagar blocos

### 2.7 Fazer Círculos

Agora testaremos os movimentos do robô, para verificar se não existe problemas de ligação na montagem do robô, primeiro utilizaremos o bloco chamado “Go in Circles” que movimentará o robô em círculos fazendo que uma roda vá para um sentido e a outra roda para o sentido oposto, para isto basta colocar os blocos no ordem mostrado na Figura 52. clicamos em “Upload to Arduíno” e o código será carregado para o Arduíno IDE.


Tutorial - iModBot@ipleiria.pt | 32

Figura 53 - Go in Circles

### 2.8 Movimentos aleatórios

Para experimentar mais movimentos do que mover em círculos, vamos fazer a próxima sequência de blocos na ferramenta “ArduBlocks”, a usar o bloco chamado “Walking Randomly” que faz com que o robô percorra movimentos aleatórios, carregamos em “Upload to Arduíno” e o robô fará a tarefa, como na Figura 54.


Tutorial - iModBot@ipleiria.pt | 33

Figura 54 - Walking Randomly

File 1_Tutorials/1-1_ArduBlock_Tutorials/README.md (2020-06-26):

# Tutoriais para Ardublock

Os presentes tutoriais deverão facilitar a compreensão da linguagem de programação por blocos.

Pode encontrar as atividades associadas em [/2_Atividades/2-1_Atividades_para_ArduBlock/](https://github.com/ipleiria-robotics/iModBot/tree/master/2_Atividades/2-1_Atividades_para_ArduBlock).

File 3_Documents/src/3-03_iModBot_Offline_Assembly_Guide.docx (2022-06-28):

GUIA DE MONTAGEM

Passo 1:

Este documento irá servir de guia para a montagem do robô iModBot@ipleiria.pt.

Como instalar o Arduino IDE:
https://www.arduino.cc/en/Guide/windows

Foi criada uma biblioteca para facilitar a programação do robô, a mesma está disponível em:
---
Passo 2:

Video demonstrativo de como instalar a biblioteca:

https://youtu.be/pUydwEE_rCo

Foi criada uma versão personalizada do Ardublocks que possui novos blocos que permitem o controlo do robô.
A mesma está disponível em:
---

Passo 3:

Video demonstrativo de como instalar o Ardublocks:

https://youtu.be/oaflX_1ZpHQ

Estabeleças as ligações como demonstrado nas imagens.

Também está disponível um vídeo que demonstra a montagem dos vários componentes:


Figura 1 - Passo 1


Figura 2 - Passo 2


Figura 3 - Passo 3


Figura 4 - Passo 4


Figura 5 - Passo 5


Figura 6 - Passo 6


Figura 7 - Passo 7


Figura 8 - Passo 8


Figura 9 - Passo 9

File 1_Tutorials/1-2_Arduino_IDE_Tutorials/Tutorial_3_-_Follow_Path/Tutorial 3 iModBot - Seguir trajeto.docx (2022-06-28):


| Tutorial – Movimento iModBot@ipleiria.pt

# Introdução

O robô EDURobot é um veículo elétrico de pequenas proporções controlado pelo microcontrolador ESP32. Este microcontrolador pode ser programado usando a linguagem C/C++ e o software gratuito Arduino IDE.

Este tutorial vai focar-se na função de seguir automaticamente um trajeto.

Para efetuar a tarefa de seguir um trajeto autonomamente é necessário verificar constantemente se há algum obstáculo a obstruir o caminho, caso haja é necessário parar os motores.

De seguida é necessário verificar os sensores infravermelho de modo a determinar o percurso que o robô deve seguir.

Embora pareca um processo simples há varias coisas a ter em conta.

O seguinte fluxograma descreve os procedimentos para executar a tarefa de seguir um trajeto (linha) autónomamente.


Seguir trajeto – exemplo 1

Exemplo:

#include <robotOnLine.h>

robotOnLine robot; // Criar um objeto chamado "robot"

void setup()

{

robot.begin(); // Configura os pinos.

robot.beginAutoDrive(); // Inicia a função de condução autónoma.

}

void loop()

{

int info = 0; // Variável para guardar o numero devolvido pela função autoDrive().

int command = 0; // variável para lembrar que comandos já foram executados.

info = robot.autoDrive(0); // Aqui copiamos o valor devolvido pela função para a variável info.

/* Sempre que usarem a função autoDrive() têm de enviar um valor, estes são as instruções aceites:

0 -> Enviar 0 ou qualquer outro número (até 255) não listado se não quiser dar instruções ao robô.

1 -> Enviar 1 para colocar o robô a rodar para a direita até encontrar uma linha.

2 -> Enviar 2 para colocar o robô a rodar para a esquerda até encontrar uma linha.

3 -> Enviar 3 para dizer ao robô para seguir em frente.

4 -> Enviar 4 para dizer ao robô para recuar, tenha em atenção que o robô pode-se desalinhar

ligeiramente devido à roda traseira.

*/

}

#### Descrição

A biblioteca “RobotOnLine” dispõe de funções que permitem facilmente implementar a tarefa de seguir um trajeto de forma autónoma.

#### Sintaxe

beginAutoDrive(); // Inicia a função de condução autónoma.

autoDrive(byte ); // Realiza tarefas necessárias para a condução autónoma.

#### Parâmetros

autoDrive( numero )

a variável número pode ter os seguintes valores:

0 sem efeito.

1 robô roda para a direita até encontrar uma linha.

2 robô a rodar para a esquerda até encontrar uma linha.

3 robô segue em frente.

4 robô recua.

A função autoDrive(byte ) pode devolver um dos seguintes valores:

1 multiplas linhas encontradas.

2 obstaculo encontrado.

3 não foram encontradas linhas.

#### Respostas

Nenhum

Seguir trajeto – exemplo 2

Exemplo:

#include <robotOnLine.h>

robotOnLine robot;

bool cruzamento = 0;

void setup()

{

robot.begin();

pinMode(LED_BUILTIN, OUTPUT);

Serial.begin(115200);

}

void loop()

{

while ( (robot.readCLP() != HIGH) && (robot.distance() > 10) )

{

if( (robot.readS2() == 0) || (robot.readS3() == 0) || (robot.readS4() == 0) )

{

if( (robot.readS2() == 1) && (robot.readS3() == 0) && (robot.readS4() == 1) )

{

robot.forward(255);

while((robot.readS2() == 1) && (robot.readS3() == 0) && (robot.readS4() == 1))

{

;

}

}

else if( (robot.readS2() == 0) && (robot.readS3() == 1) && (robot.readS4() == 1) )

{

robot.rotateLeft(255);

while((robot.readS2() == 0) && (robot.readS3() == 1) && (robot.readS4() == 1))

{

;

}

}

else if( (robot.readS2() == 1) && (robot.readS3() == 1) && (robot.readS4() == 0) )

{

robot.rotateRight(255);

while((robot.readS2() == 1) && (robot.readS3() == 1) && (robot.readS4() == 0))

{

;

}

}

else if( (robot.readS3() == 0) && (robot.readS4() == 0) && (robot.readS5() == 0) )

{ //sensores do meio e da direita detetaram uma linha

cruzamento = 1;

}

else if( (robot.readS1() == 0) && (robot.readS2() == 0) && (robot.readS3() == 0))

{ //sensores da esquerda e do meio detetaram uma linha

cruzamento = 1;

}

else if( (robot.readS1() == 0) && (robot.readS2() == 0) && (robot.readS4() == 0)

&& (robot.readS5() == 0) )

{ //sensores da esquerda e da direita detetaram uma linha

cruzamento = 1;

}

if(cruzamento == 1)

{

// Inserir código a efetuar num cruzamento, aqui.

cruzamento = 0;

}

}

digitalWrite(LED_BUILTIN, HIGH);

if( (robot.readS2() == 1) && (robot.readS3() == 1) && (robot.readS4() == 1) )

{

robot.stopMotors();

while((robot.readS2() == 1) && (robot.readS3() == 1) && (robot.readS4() == 1));

}

}

robot.stopMotors();

digitalWrite(LED_BUILTIN, LOW);

while (robot.readCLP());

}

#### Descrição

Este exemplo permite ao robô seguir um trajeto sem recorrer à função de condução autónoma disponibilizada pela biblioteca “RobotOnLine”

Note que há ciclos while() após cada instrução que afeta o movimento do robô, isto serve para impedir que a instrução seja repetida indefinidamente.

#### Sintaxe

Parâmetros

state = variável que recebe o valor da função, 1 ou 0, consoante o estado do pino.

#### Respostas

Nenhum

Tutorial – Movimento iModBot@ipleiria.pt Página 30 de 30

Politécnico de Leiria 2019/2020

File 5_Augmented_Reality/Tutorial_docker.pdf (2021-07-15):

## Docker

Guia para iniciantes


Elaborado por:
Nelson Henriques – 2190514

Orientado por:
Carlos Neves
Luís Conde

# iModBot

### Índice

V1.1 – 22/06/2021 | 1

Docker
Guia para iniciantes

### 1. Introdução

O Docker é uma ferramenta utilizada para tornar mais fácil criar, implementar e executar aplicações utilizando containers. Os containers permitem que o desenvolvedor empacote a aplicação bem como todas as partes de que precisa, como bibliotecas e outras dependências, e implemente-o como um package. Assim o desenvolvedor pode ter certeza de que a aplicação será executada em qualquer outra máquina Linux, independentemente de quaisquer configurações personalizadas que a máquina possa ter, que podem ser diferentes da máquina usada para escrever e testar o código.

De certa forma, o Docker é idêntico a uma máquina virtual. Mas, ao contrário de uma máquina virtual, em vez de criar um sistema operativo virtual completo, o Docker permite que as aplicações usem o mesmo kernel Linux do sistema em que estão a ser executadas, requer apenas que as aplicações sejam enviadas com coisas que ainda não estão a ser executadas no host. Isto possibilita um aumento significativo no desempenho e reduz o tamanho da aplicação.

Compose é uma ferramenta utilizada para definir e executar aplicações Docker compostas por vários containers. O Compose utiliza arquivos YAML para configurar os serviços da aplicação. Então, com um único comando cria e inicia todos os serviços da configuração.

1.1.Objetivos

Pretende-se com este tutorial fornecer os conhecimentos básicos para a utilização do software Docker e Docker-Compose.
Ao longo do tutorial vai-se abordar os seguintes temas:
- Terminologia Docker;
- Instalar o software Docker e Docker-Compose;
- Comandos básicos Docker.
- Comandos básicos Docker-Compose.

(Este tutorial é destinado ao Docker e Docker-Compose em um sistema Linux 20.04)

V1.1 – 22/06/2021 | 2

## 2. Terminologia Docker

2.1.Images
As images do docker são a "receita" para um container. As images contém todas as definições de como inicializar o ambiente Linux. Normalmente, uma imagem Docker existe para cumprir especificamente uma tarefa. Por exemplo, uma imagem definiria o seu servidor web e outra imagem definiria a database subjacente.

2.2.Containers
Os containers são instanciações de imagens. Eles são uma forma de imagem. Compare-a com a programação orientada a objetos, então sua classe seria uma imagem e uma instância da classe, um container. Outra comparação seria com contentores reais num cargueiro. Estes tem uma aparência idêntica por fora, mas por dentro são/podem ser completamente diferentes. Alguns factos interessantes sobre containers:
- Os containers não são persistentes. Assim que não estiverem a ser utilizados eles são desligados, ou até mesmo eliminados.
- Um container só vive enquanto um processo é executado dentro dele.
- Os containers podem incluir dados, mas estes também não são persistentes. Se quiser torná-los persistentes, pode-se utilizar volumes.
- Para comunicar entre containers, usa-se os mesmos protocolos que se usariam para comunicar entre computadores (por exemplo, TCP / IP).

2.3.Volumes
Os volumes podem ser usados como camada de dados subjacente. Estes podem ser utilizados por vários containers. Todos os dados guardados num volume podem ser acedidos por qualquer container conectado a ele.

2.4.Networks
O Docker vem com as suas próprias capacidades de networking. O nome de um container é seu nome de host. A maneira mais fácil de experimentar isso é ter dois containers em execução e executar o comando para verificar o ping em um container de dentro de outro container. O Docker Compose irá gerar sua própria sub-rede.


V1.1 – 22/06/2021 | 3

### 3. Instalar o software Docker e Docker-Compose

3.1.Docker
Iremos instalar utilizando o repositório oficial do Docker.
1. Atualize as packages do apt e adicione novas para o mesmo poder utilizar o repositório por HTTPS:

sudo apt-get update
sudo apt-get install \
apt-transport-https \
ca-certificates \
curl \
gnupg \
lsb-release
2. Adicione a chave GPG do Docker.
curl -fsSL https://download.docker.com/linux/ubuntu/gpg | sudo gpg --dearmor
-o /usr/share/keyrings/docker-archive-keyring.gpg
3. Usa o seguinte comando para criar o repositório local.

echo \
"deb [arch=amd64 signed-by=/usr/share/keyrings/docker-archive-keyring.gpg] https://download.docker.com/linux/ubuntu \
$(lsb_release -cs) stable" | sudo tee /etc/apt/sources.list.d/docker.list >
/dev/null
4. Instale o Docker.

sudo apt-get update
sudo apt-get install docker-ce docker-ce-cli containerd.io
5. Verifique se o Docker foi instalado corretamente..

docker --version

deverá obter algo semelhante á Figura 1

Figura 1 - Versão do Docker.


V1.1 – 22/06/2021 | 4

3.2.Docker-Compose

### 1. Descarregue a versão mais recente e estável do Docker-Compose

sudo curl -L
"https://github.com/docker/compose/releases/download/1.29.1/docker-compose-$(uname -s)-$(uname -m)" -o /usr/local/bin/docker-compose
2. Dê permissão de execução ao binário descarregado.

sudo chmod +x /usr/local/bin/docker-compose

3. Verifique se o Docker-Compose foi instalado corretamente.

docker-compose --version

Deverá obter algo semelhante á Figura 1

Figura 2 - Versão do Docker-Compose.


V1.1 – 22/06/2021 | 5

### 4. Comandos básicos Docker

1. Iremos começar correndo o clássico “Hello World”.

docker run hello-world

Deverás obter a seguinte resposta (Figura 3).

Figura 3 - Output de "Hello World"
A output já descreve muito bem o que acontece ao executar este comando.
Iniciou-se um container, cujo a imagem foi descarregada do Docker hub, de seguida executou-o e enviou a resposta para o terminal.
2. Vê todos os containers que estão em execução ou foram executados.

docker ps -a

Figura 4 - containers que estão em execução ou foram executados
Os “Names” são gerados aleatoriamente, podemos referir-nos aos containers pelos “Names” ou pelo “container id” (Figura 4)


V1.1 – 22/06/2021 | 6

### 3. Execute novamente o “Hello World” mas desta vez iremos atribuir um nome, assim não

dependemos de um nome gerado aleatoriamente.

docker run --name My-HW hello-world

### 4. Execute novamente o comando do passo nº2 e verifique que o nome é igual ao que foi

atribuído no comando anterior (Figura 5).

Figura 5 - container com o nome customizado

### 5. Agora vamos executar um container que contem o ubunto (como este container não está

localmente o Docker ira descarrega-lo do Docker Hub)e ao mesmo tempo iremos atribuir um nome customizado

docker run -it --name my-linux-container ubuntu bash

Figura 6 - ubunto container

Agora está dentro do container ubunto (Figura 6) onde pode executar qualquer comando Linux isto é bastante útil quando estamos num sistema windows ou macOS, para sair basta escrever “exit”.

6. Mais uma vez ao executar o comando do passo nº2 para ver o estado de todos os containers executados ou em execução ate ao momento (Figura 7).

Figura 7 - Containers executados ou em execução


V1.1 – 22/06/2021 | 7
7. Verifique quais as imagens que tem guardados localmente.

docker images

Figura 8 - docker images
Este comando pode ser bastante útil pois permite saber todas as informações principais das “images” (Figura 8), como estão guardados localmente a sua execução da próxima vez será instantânea.

### 8. Uma vez iniciado um container com um nome pré-definido pelo utilizador o mesmo já não

pode ser iniciado com o mesmo nome, por isso podemos executar o seguinte comando de modo a limpar o “histórico” de containers executados (Figura 9).

docker rm $(docker ps -a -f status=exited -q)

Figura 9 - output
9. Verifique que a lista está limpa correndo o comando do passo nº2.

### 10. Inicie um container e ao mesmo tempo conecte-o a uma pasta local, para isso crie uma

pasta no seu sistema operativo local e guarde o seu caminho, substituindo-o no comando abaixo.

docker run -it --name my-linux-container --rm -v [diretoria local] ubuntu bash

- -it (interactive container) – entra no mesmo assim que inicia.
- --rm – assim que termina elimina-o da lista.
- -v – comando para conectar a diretoria local sendo que a pasta a partilhar tem que anteceder “:”. Ex:
docker run -it --name my-linux-container --rm -v /home/ipleiria/Desktop:/meus_dados ubuntu bash


V1.1 – 22/06/2021 | 8
11. Verifique que a pasta foi partilhada executando o comando ls dentro do container.

Figura 10 - pasta partilhada
Como pode observar a pasta foi partilhada corretamente (Figura 10).

### 12. Execute um comando no container ubuntu, para isso, abra um novo terminal (não feche o

atual), e utilize o seguinte código.

docker exec -it my-linux-container echo "Hello World"

Com este código irá imprimir um Hello World (Figura 11), sendo que depois do nome do container vem o comando a executar no mesmo.

Figura 11 - comando executado

### 13. Crie um Docker image, para isso crie uma nova pasta e atribua-lhe o nome “My-Docker-

Image”, dentro dessa pasta crie um ficheiro com o nome “Dockerfile” (certifique-se que não tem um tipo de ficheiro ex: .txt), abra-o com um editor de texto, neste momento deverá ter algo semelhante á Figura 12.

Figura 12 - ficheiro Dockerfile

14. No ficheiro escreva as seguintes linhas de código (Figura 13), guarda e fecha o ficheiro.

Figura 13 - código a escrever


V1.1 – 22/06/2021 | 9

Existe uma grande variedade de “Keywords” para criar imagens Docker estas podem ser encontradas aqui: https://docs.docker.com/engine/reference/builder/.

15. No terminal vá á diretoria criada (esta diretoria varia dependendo de onde criou a pasta).

cd /home/ipleiria/Desktop/My-Docker-Image

16. Construa a imagem.

docker build -t my-ubuntu-image .

- -t – atribui um nome á imagem.

Deverá obter algo semelhante á Figura 14.

Figura 14 - imagem criada

17. Verifique que a imagem foi criada (Figura 15).

docker images

Figura 15 - lista de imagens locais


V1.1 – 22/06/2021 | 10
18. Corra a imagem criada.

docker run my-ubuntu-image

Figura 16 - output do meu container
Como pode observar ao executar o container ele escreveu no terminal o que foi escrito no Dockerfile (Figura 16).
Ex:
Pretende iniciar um ubuntu Docker já com o python3 instalado, para isso no ficheiro criado anteriormente basta trocar o “CMD echo "Hello World - From My Container"” por “RUN apt-get upgrade && apt-get update && apt-get install -y python3” e contruir novamente a imagem, assim terá uma imagem ubunto com o python3 já instalado.

Pode também guardar o estado do seu container em uma nova imagem através do seguinte comando:
docker commit $CONTAINER_ID image name


V1.1 – 22/06/2021 | 11

### 5. Comandos básicos Docker-Compose

1. Descarregue o conteúdo do repositório, este será o exemplo utilizado para o tutorial. (https://github.com/jakewright/tutorials/tree/master/docker/02-docker-compose)

Nessa pasta irás encontrar 4 ficheiros, “product”, “Website”, “readme.md” e “Docker-compose.yml”, o ficheiro “Docker-compose.yml” é o ficheiro onde estão todas as definições da aplicação, que neste caso é um web site muito simples.
Este exemplo está pronto a ser executado mas antes disso iremos entender o que irá o ficheiro “Docker-compose.yml” fazer.
2. Abra o ficheiro “Docker-compose.yml” com o seu editor preferido (Figura 17).

Figura 17- Docker-Compose.yml
Version: – Versão em que está a ser escrita o ficheiro (opcional a partir da versão 1.27). services: – serviços a iniciar.
Product-service e website – nome dos serviços.

O restante são as dependências e definições dos serviços sendo que tem que ser adaptadas ao que pretende realizar, para mais informação consulte este link: https://docs.docker.com/compose/compose-file/

3. Abra o terminal e vá até á diretoria descarregada.

cd /home/ipleiria/Desktop/02-docker-compose/


V1.1 – 22/06/2021 | 12
4. Agora irá “construir” a aplicação com base no ficheiro criado (Figura 18).

docker-compose build

Figura 18 - construção terminada

5. Agora irá iniciar a aplicação criada (Figura 19).

docker-compose up

Figura 19 - aplicação iniciada

6. Aceda a localhost:5000 no seu browser, deverá aparecer algo semelhante á Figura 20.

Figura 20 - website exemplo


V1.1 – 22/06/2021 | 13

Caso dê um erro semelhante ao da Figura 21, corra o seguinte comando:
sudo chmod 755 website

Figura 21 - possivel erro

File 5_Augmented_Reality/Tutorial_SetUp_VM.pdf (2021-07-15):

## SetUp Virtual Machine

xubuntu


Elaborado por:
Nelson Henriques – 2190514

Orientado por:
Carlos Neves
Luís Conde

# iModBot

### Índice

V1.1 – 22/06/2021 | 1

Set Up Virtual Machine
xubuntu

### 1. Introdução

VirtualBox é um software de virtualização desenvolvido pela empresa Innotek e comprado pela empresa Oracle que, como o VMware Workstation, visa criar ambientes para instalação de sistemas distintos. Este permite a instalação e utilização de um ou mais sistemas operacionais dentro de outro, assim como seus respetivos softwares, como dois ou mais computadores independentes, mas partilham fisicamente o mesmo hardware.

1.1.Objetivos

Pretende-se com este tutorial guiar qualquer pessoa na criação de uma Virtual Machine dedicada ao ROS2 utilizando o software VirtualBOX. Ao longo do tutorial vai-se abordar os seguintes temas:
- Criar uma VM (xubuntu-20.04);
- Configurações;
- Instalar GuestAdditions.

(Este tutorial pressupõe que já tem instalado o VirtualBox, todos os comandos utilizados têm como utilizador ipleiria, tendo que ser substituído pelo seu nome de utilizador, download do xubuntu-20.04 – http://ftp.uni-kl.de/pub/linux/ubuntu-dvd/xubuntu/releases/20.04/release/xubuntu-20.04.2.0-desktop-amd64.iso)
)


V1.1 – 22/06/2021 | 2

### 2. Criar uma VM

1. Abra o virtual box e clique em New (Figura 1).

Figura 1 - New virtual machine
2. Dá um nome á tua maquina virtual, escolhe o local onde será isntalada e seleciona o tipo de sistema operativo e a arquitetura (32 ou 64 bits) (Figura 2).

Figura 2 - Seleção do nome e sistema operativo


V1.1 – 22/06/2021 | 3

### 3. Selecione a quantidade de Ram para dedicar á maquina virtual cerca de 1/3 da memoria

do seu computador (Figura 3).

Figura 3 – Ram dedicada

4. Crie um novo disco virtual (Figura 4).

Figura 4 - Criar um disco virtual


V1.1 – 22/06/2021 | 4

### 5. Selecione VDI (Figura 5)

Figura 5 - VDI

### 6. Selecione “Dynamically allocated” assim o disco virtual irá aumentar de tamanho

consoante a sua utilização (Figura 6).

Figura 6 - Dynamically allocated


V1.1 – 22/06/2021 | 5
7. Escolha a capacidade do disco, é preferível escolher um valor grande pois o disco virtual só irá ocupar o espaço que necessita (Figura 7), e faça “Create”.

Figura 7 - Tamanho do disco virtual
8. Selecione a maquina virtual criada e vá a “Settings” (Figura 8).

Figura 8 - Máquina criada


V1.1 – 22/06/2021 | 6
9. Vá a “Storage” e selecione o disco “Empty” e selecione o ficheiro .iso (Figura 9).

Figura 9 - Definições de Storage

### 10. Em “Network” mude “Attached to:” para “Bridge adapter” e de seguida selecione o seu

adaptador (Figura 10).

Figura 10 – Definições de Network


V1.1 – 22/06/2021 | 7

2.1.Instalar Guest Additions

1. Vá a “Devices” e clique em “Insert Guest Additions CD image” (Figura 11).

Figura 11 – Inserir o disco virtual Guest Additions

### 2. Agora corra os seguintes comandos no terminal (a versão poderá ter que ser

alterada)(Figura 12).

cd /media/ipleiria/VBox_GAs_6.1.20/
sudo ./autorun.sh

Figura 12 – Instalando as Guest Additions

V1.1 – 22/06/2021 | 8
3. Ao terminar a instalação reinicie a máquina virtual.

A instalação está concluída.

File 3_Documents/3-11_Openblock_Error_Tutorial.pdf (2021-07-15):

# Tutorial

# Erro na Instalação do Openblocks

Elaborado por:
Abel Teixeira – 2180522
Samuel Lourenço – 2180356

Verificado por:
Marco Pereira – 2190516
Nelson Henriques – 2190514

Orientado por:
Carlos Neves
Luís Conde

# iModBot

### ÍNDICE


V1.1 – 23/06/2021 | 1

Tutorial
Erro na Instalação do Openblocks

## INTRODUÇÃO

Pode acontecer que no momento de executar o seguinte comando “mvn install”, para instalar o Openblocks no projeto Ardublock, que lhe surja um erro semelhante ao da Figura 1, que indica que a versão do java não é suportada.
Neste momento já deve ter executado todos os passos do tutorial “Editar_Ardublock_com_Eclipse”, até ao passo 5.6 (inclusive).

Figura 1 - Erro ao executar o comando “mvn install”


V1.1 – 23/06/2021 | 2

### 1. Abrir o ficheiro “pom”

Na pasta “Ardublock-Workspace”, entrar na pasta “openblocks-master” e abrir o ficheiro “pom” com o Bloco de notas ou Notepad++ (Figura 2).

Figura 2 – Abrir o ficheiro “pom”


V1.1 – 23/06/2021 | 3

### 2. Localizar a versão

Procure por as linhas de texto “<source> 1.6 </source>” e “<target> 1.6 </target>”, geralmente localizadas nas linhas 24 e 25 (Figura 3).

Figura 3 – Localizar a versão


V1.1 – 23/06/2021 | 4

### 3. Alterar os valores

Após localizar os valores, deve de alterá-los de “1.6” para “1.8”, ficando com o aspeto da Figura
4. De seguida pode guardar o ficheiro e fechá-lo.

Figura 4 – Alterar os valores


V1.1 – 23/06/2021 | 5

### 4. Instalar o Openblocks

Neste momento, pode voltar a instalar o Openblocks no projeto Ardublock, executando o comando “mvn install” na PowerShell. Deverá ser instalado com sucesso aparecendo uma mensagem idêntica à da Figura 5.

Figura 5 – Instalar o Openblocks

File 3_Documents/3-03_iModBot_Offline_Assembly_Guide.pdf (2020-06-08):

Este documento irá servir de guia para a montagem do robô iModBot@ipleiria.pt.

Como instalar o Ardiono IDE:
https://www.arduino.cc/en/Guide/windows

Foi criada uma biblioteca para facilitar a programação do robô, a mesma está disponível em:

Video demonstrativo de como instalar a biblioteca:

https://youtu.be/pUydwEE_rCo

Foi criada uma versão personalizada do Ardublocks que possui novos blocos que permitem o controlo do robô.
A mesma está disponível em:

Video demonstrativo de como instalar o Ardublocks:

https://youtu.be/oaflX_1ZpHQ

Estabeleças as ligações como demonstrado nas imagens.

Também está disponível um vídeo que demonstra a montagem dos vários componentes:


Figura 1 - Passo 1


Figura 2 - Passo 2


Figura 3 - Passo 3


Figura 4 - Passo 4


Figura 5 - Passo 5


Figura 6 - Passo 6


Figura 7 - Passo 7

Figura 8 - Passo 8


Figura 9 - Passo 9

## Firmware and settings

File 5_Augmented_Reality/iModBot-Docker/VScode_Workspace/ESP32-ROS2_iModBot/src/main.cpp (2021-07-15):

#include <Arduino.h>
#include <ros2arduino.h>
#include <WiFi.h>
#include <WiFiUdp.h>
#include <iModBot.h>

#define SSID "nome da rede wifi"
#define SSID_PW "pass da rede wifi"
#define AGENT_IP "ip do agente"
#define AGENT_PORT 2018 //AGENT port number

#define SENSORS_UPDATE_FREQ 20 //hz

iModBot robot;
float Linear, Angular;

void US_sensor_dist(std_msgs::Int16 *msg, void *arg)
{
  (void)(arg);

  msg->data = robot.distance();
}

void IR_board_sensors(std_msgs::String *msg, void *arg)
{
  (void)(arg);

  sprintf(msg->data, "%d,%d,%d,%d,%d,%d,%d", robot.readS1(), robot.readS2(), robot.readS3(), robot.readS4(), robot.readS5(), robot.readCLP(), robot.readNear());
}

void Enc_count_RL(std_msgs::String *msg, void *arg)
{
  (void)(arg);

  sprintf(msg->data, "%d,%d", robot.getRightEncoderCount(), robot.getLeftEncoderCount());
}

class PubSensors : public ros2::Node
{
public:
  ros2::Publisher<std_msgs::Bool> *on_col;
  PubSensors()
      : Node("PubSensors_node")
  {
    on_col = this->createPublisher<std_msgs::Bool>("col_flag");

    ros2::Publisher<std_msgs::Int16> *US_sensor = this->createPublisher<std_msgs::Int16>("US_sensor_dist");
    this->createWallFreq(SENSORS_UPDATE_FREQ, (ros2::CallbackFunc)US_sensor_dist, nullptr, US_sensor);

    ros2::Publisher<std_msgs::String> *IR_board = this->createPublisher<std_msgs::String>("IR_board_sensors");
    this->createWallFreq(SENSORS_UPDATE_FREQ, (ros2::CallbackFunc)IR_board_sensors, nullptr, IR_board);

    ros2::Publisher<std_msgs::String> *Enc_count = this->createPublisher<std_msgs::String>("Enc_count_RL");
    this->createWallFreq(SENSORS_UPDATE_FREQ, (ros2::CallbackFunc)Enc_count_RL, nullptr, Enc_count);
  }
};

void subscribeCMD_Vel(geometry_msgs::Twist *cmd_vel, void *arg)
{
  (void)(arg);

  Linear = cmd_vel->linear.x;
  Angular = cmd_vel->angular.z;
}

class SubCMD_Vel : public ros2::Node
{
public:
  SubCMD_Vel()
      : Node("CMD_Vel_sub_node")
  {
    this->createSubscriber<geometry_msgs::Twist>("cmd_vel_SOC", (ros2::CallbackFunc)subscribeCMD_Vel, nullptr);
  }
};

WiFiUDP udp;

void setup()
{
  Serial.begin(115200);
  WiFi.begin(SSID, SSID_PW);
  Serial.print("Connecting");
  while (WiFi.status() != WL_CONNECTED)
  {
    Serial.println(".");
    delay(100);
  }
  Serial.print("Connected");
  ros2::init(&udp, AGENT_IP, AGENT_PORT);

  robot.begin();
}

void loop()
{
  static std_msgs::Bool col_flag;

  static PubSensors pubNode;
  static SubCMD_Vel CMD_Vel_Sub_Node;

  ros2::spin(&CMD_Vel_Sub_Node);
  ros2::spin(&pubNode);

  //-------------robotmovment-------------
  int botspeed_fb = 180;
  int botspeed_rl = 160;
  if (Linear > 0)
  {
    robot.forward(botspeed_fb);
  }

  if (Linear < 0)
  {
    robot.reverse(botspeed_fb);
  }

  if (Angular > 0)
  {
    robot.rotateRight(botspeed_rl);
  }

  if (Angular < 0)
  {
    robot.rotateLeft(botspeed_rl);
  }

  if (Linear == 0 && Angular == 0)
  {
    robot.stopMotors();
  }

  //----------------coldetect----------------
  static bool lastS = 0;
  if (robot.readCLP() == 1 && lastS == 0)
  {
    lastS = 1;
    col_flag.data = true;
    pubNode.on_col->publish(&col_flag);
  }

  if (robot.readCLP() == 0 && lastS == 1)
  {
    lastS = 0;
  }
}

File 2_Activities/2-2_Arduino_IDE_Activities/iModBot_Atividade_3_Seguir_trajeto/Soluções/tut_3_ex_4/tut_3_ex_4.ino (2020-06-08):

#define CLP 39
#define Near 36
#define S1 25
#define S2 33
#define S3 32
#define S4 35
#define S5 34

bool cruzamento = 0;
byte count = 0;

void setup()
{
  pinMode( 4,OUTPUT); //Direita
  pinMode(16,OUTPUT); //Direita
  pinMode(17,OUTPUT); //Esquerda
  pinMode(18,OUTPUT); //Esquerda
  pinMode(LED_BUILTIN, OUTPUT);

  Serial.begin(115200);
}

void loop()
{
  while ( (digitalRead(CLP) != HIGH)  && (distancia() > 10) )
  {
    if( (digitalRead(S2) == 0) || (digitalRead(S3) == 0) || (digitalRead(S4) == 0) )
    {
      if( (digitalRead(S2) == 1) && (digitalRead(S3) == 0) && (digitalRead(S4) == 1) )
      {
        frente();
        while((digitalRead(S2) == 1) && (digitalRead(S3) == 0) && (digitalRead(S4) == 1))
        {
          ;
        }
      }
      else if( (digitalRead(S2) == 0) && (digitalRead(S3) == 1) && (digitalRead(S4) == 1) )
      {
        esquerda();
        while((digitalRead(S2) == 0) && (digitalRead(S3) == 1) && (digitalRead(S4) == 1))
        {
          ;
        }
      }
      else if( (digitalRead(S2) == 1) && (digitalRead(S3) == 1) && (digitalRead(S4) == 0) )
      {
        direita();
        while((digitalRead(S2) == 1) && (digitalRead(S3) == 1) && (digitalRead(S4) == 0))
        {
          ;
        }
      }
      else if( (digitalRead(S3) == 0) && (digitalRead(S4) == 0) && (digitalRead(S5) == 0) )
      { //sensores do meio e da direita detetaram uma linha
        cruzamento = 1;
        count++;
      }
      else if( (digitalRead(S1) == 0) && (digitalRead(S2) == 0) && (digitalRead(S3) == 0))
      { //sensores da esquerda e do meio detetaram uma linha
        cruzamento = 1;
        count++;
      }
      else if( (digitalRead(S1) == 0) && (digitalRead(S2) == 0) && (digitalRead(S4) == 0) 
      && (digitalRead(S5) == 0) )
      { //sensores da esquerda e da direita detetaram uma linha
        cruzamento = 1;
        count++;
      }

      if(cruzamento == 1)
      {
        switch(count)
        {
          case 1:
            direita();
            while(digitalRead(S3)==0);
            while(digitalRead(S3)==1);
            pararMotores();
            break;
            
          case 2:
            esquerda();
            while(digitalRead(S3)==0);
            while(digitalRead(S3)==1);
            pararMotores();
            break;
            
          case 3:
            esquerda();
            while(digitalRead(S3)==0);
            while(digitalRead(S3)==1);
            pararMotores();
            break;
            
          default:
            break;
        }
        
        cruzamento = 0;
      }
    }
    
    digitalWrite(LED_BUILTIN, HIGH);
    
    if( (digitalRead(S2) == 1) && (digitalRead(S3) == 1) && (digitalRead(S4) == 1) )
    {
      pararMotores();
      while((digitalRead(S2) == 1) && (digitalRead(S3) == 1) && (digitalRead(S4) == 1));
    }
  }
  pararMotores();

  digitalWrite(LED_BUILTIN, LOW);

  while (digitalRead(CLP));
}

byte distancia()
{
  digitalWrite(14, LOW);
  delayMicroseconds(2);

  digitalWrite(14, HIGH);
  delayMicroseconds(10);
  digitalWrite(14, LOW);

  uint32_t duration = pulseIn(12, HIGH);

  uint dist = int(duration * 0.034f / 2.f);
  if (dist > 255)
  {
    return 255;
  }
  else
  {
    return dist;
  }
}

void frente()
{
  digitalWrite( 4, LOW);
  digitalWrite(16, HIGH);

  digitalWrite(17, HIGH);
  digitalWrite(18, LOW);
}

void recuar()
{
  digitalWrite( 4, HIGH);
  digitalWrite(16, LOW);

  digitalWrite(17, LOW);
  digitalWrite(18, HIGH);
}

void direita()
{
  digitalWrite( 4, HIGH);
  digitalWrite(16, LOW);

  digitalWrite(17, HIGH);
  digitalWrite(18, LOW);
}

void esquerda()
{
  digitalWrite( 4, LOW);
  digitalWrite(16, HIGH);

  digitalWrite(17, LOW);
  digitalWrite(18, HIGH);
}

void pararMotores()
{
  digitalWrite( 4, LOW);
  digitalWrite(16, LOW);

  digitalWrite(17, LOW);
  digitalWrite(18, LOW);
}

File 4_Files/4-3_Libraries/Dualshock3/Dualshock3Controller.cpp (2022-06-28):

#include <Dualshock3Controller.h>

// #define DEBUG 1
// #define TIMINGS_ACCEL 1
// #define TIMINGS_DECEL 1

Dualshock3Controller::Dualshock3Controller(uint8_t motor_pin_1,
                                           uint8_t motor_pin_2,
                                           uint8_t motor_pin_3,
                                           uint8_t motor_pin_4,
                                           uint8_t trig_pin,
                                           uint8_t echo_pin,
                                           uint8_t led_pin,
                                           uint8_t resolution,
                                           uint16_t frequency,
                                           uint8_t rampIntervalAcel,
                                           uint8_t rampIntervalDecel,
                                           uint8_t max_speed,
                                           uint8_t min_speed,
                                           uint8_t rotate_speed,
                                           uint8_t DEADZONE,
                                           float steeringSensivity)
{
  this->motor_pin_1 = motor_pin_1;
  this->motor_pin_2 = motor_pin_2;
  this->motor_pin_3 = motor_pin_3;
  this->motor_pin_4 = motor_pin_4;
  this->trig_pin = trig_pin;
  this->echo_pin = echo_pin;
  this->led_pin = led_pin;
  this->resolution = resolution;
  this->frequency = frequency;
  this->rampIntervalAcel = rampIntervalAcel;
  this->rampIntervalDecel = rampIntervalDecel;
  this->max_speed = max_speed;
  this->min_speed = min_speed;
  this->rotate_speed = rotate_speed;
  this->DEADZONE = DEADZONE;
  this->steeringSensivity = steeringSensivity;
  Dualshock3Controller::init();

#ifdef DEBUG
  Serial.begin(115200);
  pins_settings();
#endif
}

Dualshock3Controller::~Dualshock3Controller()
{
}

void Dualshock3Controller::init()
{
  pinMode(led_pin, OUTPUT);            // LED Built-in ESP32-DevKitC-V1
  pinMode(motor_pin_1, OUTPUT);        // Right -
  pinMode(motor_pin_2, OUTPUT);        // Right +
  pinMode(motor_pin_3, OUTPUT);        // Left -
  pinMode(motor_pin_4, OUTPUT);        // Left +
  pinMode(trig_pin, OUTPUT);           // HC-SR04 Trigger
  pinMode(echo_pin, INPUT);            // HC-SR04 Echo
  ledcSetup(0, frequency, resolution); // (PWM Channel 0, Frequency, Resolution)
  ledcAttachPin(motor_pin_1, 0);       // (Pin, PWM Channel)
  ledcSetup(1, frequency, resolution); // (PWM Channel 1, Frequency, Resolution)
  ledcAttachPin(motor_pin_2, 1);       // (Pin, PWM Channel)
  ledcSetup(2, frequency, resolution); // (PWM Channel 2, Frequency, Resolution)
  ledcAttachPin(motor_pin_3, 2);       // (Pin, PWM Channel)
  ledcSetup(3, frequency, resolution); // (PWM Channel 3, Frequency, Resolution)
  ledcAttachPin(motor_pin_4, 3);       // (Pin, PWM Channel)
}

void Dualshock3Controller::pins_settings()
{
  Serial.println(led_pin);
  Serial.println(motor_pin_1);
  Serial.println(motor_pin_2);
  Serial.println(motor_pin_3);
  Serial.println(motor_pin_4);
  Serial.println(trig_pin);
  Serial.println(echo_pin);
  Serial.println(frequency);
  Serial.println(resolution);
  Serial.println(rampIntervalAcel);
  Serial.println(rampIntervalDecel);
  Serial.println(max_speed);
  Serial.println(min_speed);
  Serial.println(DEADZONE);
  Serial.println(steeringSensivity);
}

void Dualshock3Controller::drive()
{
  if (!disableUltrasonicSensor)
  {
    distanceSR04();
    if (distance < stopDistance)
    {
      flushVar();
      move();
      reverse_start = true;
    }
    while (reverse_start == true)
    {
      speed = min_speed;
      state = 2;
      move();
      distanceSR04();
      if (distance > stopDistance)
      {
        reverse_start = false;
        flushVar();
        move();
      }
    }
  }

  if (Ps3.data.button.cross)
  {
    if (state == 2 && speed > idle)
    {
      can_accelerate = false;
      speed--;
    }
    else if (speed <= idle)
      can_accelerate = true;
    if (can_accelerate)
      state = 1;
    startDecelerate = false;
    startAccelerate = true;
  }
  else if (Ps3.event.button_up.cross)
  {
    startDecelerate = true;
    startAccelerate = false;
    can_accelerate = true;
    if (speed != max_speed)
      flushTimings();
  }

  if (Ps3.data.button.square)
  {
    if (state == 1 && speed > idle)
    {
      can_accelerate = false;
      speed--;
    }
    else if (speed <= idle)
      can_accelerate = true;
    if (can_accelerate)
      state = 2;
    startDecelerate = false;
    startAccelerate = true;
  }
  else if (Ps3.event.button_up.square)
  {
    startDecelerate = true;
    startAccelerate = false;
    can_accelerate = true;
    if (speed != max_speed)
      flushTimings();
  }

  if (Ps3.data.analog.button.r2)
  {
    if (state == 2 && speed > idle)
    {
      can_accelerate = false;
      speed--;
    }
    else if (speed <= idle)
      can_accelerate = true;
    if (can_accelerate)
      state = 1;
    startDecelerate = false;
    startAccelerateAnalog = true;
    analogSpeed = map(Ps3.data.analog.button.r2, 0, 255, min_speed, max_speed);
  }
  else if (Ps3.event.button_up.r2)
  {
    startDecelerate = true;
    startAccelerateAnalog = false;
    can_accelerate = true;
    if (speed != max_speed)
      flushTimings();
  }

  if (Ps3.data.analog.button.l2)
  {
    if (state == 1 && speed > idle)
    {
      can_accelerate = false;
      speed--;
    }
    else if (speed <= idle)
      can_accelerate = true;
    if (can_accelerate)
      state = 2;
    startDecelerate = false;
    startAccelerateAnalog = true;
    analogSpeed = map(Ps3.data.analog.button.l2, 0, 255, min_speed, max_speed);
  }
  else if (Ps3.event.button_up.l2)
  {
    startDecelerate = true;
    startAccelerateAnalog = false;
    can_accelerate = true;
    if (speed != max_speed)
      flushTimings();
  }

  if (startAccelerateAnalog)
    accelerateAnalog();
  if (startAccelerate)
    accelerate();
  if (startDecelerate)
    decelerate();

  steering();
  speed_left_motor = speed - (steer_left / (float)steeringSensivity);
  speed_right_motor = speed - (steer_right / (float)steeringSensivity);
  move();

#ifdef DEBUG
  // Serial.printf("Speed: %d\t steer_left: %d\t steer_right: %d\n\r", speed, steer_left, steer_right);
  Serial.printf("Left motor: %d\t Right motor: %d\t Driving state: %d\t Accelerate: %d\t Decelerate: %d\n\r", speed_left_motor, speed_right_motor, state, startAccelerate, startDecelerate);
#endif
}

void Dualshock3Controller::accelerate()
{
  uint32_t currentTime = millis();
  if (rampIntervalAcel > 0)
  {
    if ((currentTime - previousTimeAcel) >= rampIntervalAcel)
    {
      previousTimeAcel = currentTime;
      if (can_accelerate)
      {
        if (speed < min_speed)
          speed = min_speed;
        else if (speed != max_speed)
          speed++;
      }
    }
  }
  else
    speed = 255;
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

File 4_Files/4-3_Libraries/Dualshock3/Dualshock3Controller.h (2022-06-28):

#ifndef DUALSHOCK3CONTROLLER_H
#define DUALSHOCK3CONTROLLER_H

#include <Arduino.h>
#include <Ps3Controller.h>

// #define DEBUG 1

class Dualshock3Controller
{
private:
  uint8_t motor_pin_1, motor_pin_2, motor_pin_3, motor_pin_4; // Motor pins
  uint8_t trig_pin, echo_pin;                                 // HC-SR04 pins
  uint8_t led_pin;                                            // Built-in LED
  uint8_t DEADZONE;                                           // Deadzone for analog sticks
  uint8_t rampIntervalAcel = 0;                               // Increase speed var by 1 every 'x' ms
  uint8_t rampIntervalDecel = 0;                              // Decrease speed var by 1 every 'x' ms
  uint8_t max_speed;                                          // Maximum PWM speed
  uint8_t min_speed;                                          // Minimum PWM speed at which robot can move
  uint8_t rotate_speed;                                       // Speed at which robot rotates
  uint8_t resolution;                                         // Resolution for PWM
  uint16_t frequency;                                         // Frequency for PWM
  float steeringSensivity;                                    // Closer to 0 means more steering applied

public:
  uint8_t state; // Controls motor states. 5 in total
                 /*
                   State:
                   0 - Stop
                   1 - Forward
                   2 - Reverse
                   3 - Rotate left
                   4 - Rotate right
                 */

  bool can_accelerate = true;                          // Ready to accelerate
  bool reverse_start = false;                          // Start reverse HC-SR04
  bool startDecelerate = false;                        // Allows the robot to decelerate
  bool startAccelerate = false;                        // Allows the robot to accelerate
  bool startAccelerateAnalog = false;                  // Accelerate but for analogs
  bool drivingStyle = false;                           // Switch between driving styles
  bool disableUltrasonicSensor = true;                 // Set "true" to disable this module. Set "false" to enable this module.
  uint32_t previousTimeAcel = 0;                       // Variables for ramp generator
  uint32_t previousTimeDecel = 0;                      // Variables for ramp generator
  uint8_t speed = 0;                                   // Data that is used in formulas for the motors
  uint8_t old_speed = 0;                               // Save old speed to steering
  uint8_t idle = 0;                                    // Current smoother
  uint8_t steer_right = 0, steer_left = 0;             // Variables for steering
  uint8_t speed_left_motor = 0, speed_right_motor = 0; // Variables for motors PWM
  uint8_t analogSpeed;                                 // Converted mapping data from analog triggers
  int8_t left_analog_x;                                // Raw data from left analog stick in X-axis
  uint8_t r2, l2;                                      // Raw data from analog triggers
  uint8_t distance;                                    // HC-SR04 distance acquired from object
  int32_t duration;                                    // HC-SR04 wave travel duration
  uint8_t stopDistance = 10;                           // Distance at which robot will stop and perform given actions

  Dualshock3Controller(uint8_t motor_pin_1,
                       uint8_t motor_pin_2,
                       uint8_t motor_pin_3,
                       uint8_t motor_pin_4,
                       uint8_t trig_pin,
                       uint8_t echo_pin,
                       uint8_t led_pin,
                       uint8_t resolution,
                       uint16_t frequency,
                       uint8_t rampIntervalAcel,
                       uint8_t rampIntervalDecel,
                       uint8_t max_speed,
                       uint8_t min_speed,
                       uint8_t rotate_speed,
                       uint8_t DEADZONE,
                       float steeringSensivity);
  ~Dualshock3Controller();

  void init();
  void pins_settings();

  void drive();
  void accelerate();
  void accelerateAnalog();
  void decelerate();
  void steering();
  void features();
  void move();
  void flushVar();
  void flushTimings();
  void distanceSR04();
};

#endif

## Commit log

2020-06-08 new files upload
    [untitled.brd, untitled.sch]
2020-06-12 content match
    [untitled.brd, untitled.sch]
2020-06-25 Eagle project update
    [untitled.brd, untitled.sch]
2021-07-15 Update documentacao
    [3-7_Listagem_de_componentes_mais_links_de_compra_auxiliares.xlsx]
2021-07-15 add realidade aumentada
    [common_properties.urdf, crazyflie.skp, crazyflie.urdf.xacro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]
2022-06-28 update documents
    Added various documents
    Added source docx files
    [3-00_iModBot_Components_List.xlsx, 3-7_Listagem_de_componentes_mais_links_de_compra_auxiliares.xlsx]
2022-06-28 update files
    Added PCB Files
    Added battery case files
    Added ArduBlock files
    Added libraries
    Update readme file
    [Battery_Holder.skp, Battery_Holder_Cover_V5.stl, Battery_Holder_Slot.skp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]
2022-06-28 update AR
    Update folder
    [common_properties.urdf, crazyflie.skp, crazyflie.urdf.xacro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]
2022-07-02 update files
    [Battery_Holder.skp, Battery_Holder_Cover_V5.stl, Battery_Holder_Slot.skp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]
2022-07-02 side support motor
    [motors_side_support_v3.stl]
2022-07-04 pcb v1.2
2022-07-07 pcb v1.3
    Adjusted 3PDT Switch
    Top Silk holes
    Testpoint features charge voltage
    Text size increased
    Battery text moved
    Added text logic shifter
2022-07-07 pcb v1.31
2022-07-10 PCB v1.03.4
2022-07-13 UWB ILS
    Ultra-Wideband Indoor Location System
    [app_bar_main.xml, ic_app_icon.xml, ic_app_icon_white.xml]
2022-07-13 esp32-mdek workspace
2022-07-13 esp32-mdek UART
